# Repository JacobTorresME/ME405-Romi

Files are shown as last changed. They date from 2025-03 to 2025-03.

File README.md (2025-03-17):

# Mechatronics Romi Project
A MycroPython-based Romi robot project using an STM32 board (via the 'pyb' module). 

**By Jacob Torres and Carter Josef**

## Table of Contents
- [Overview & Objectives](#overview--objectives)
- [Features](#features)
- [Bill of Materials (BOM)](#bill-of-materials-bom)
- [Electrical Design](#electrical-design)
- [Mechanical Design](#mechanical-design)
- [Motor Characterization](#motor-characterization)
- [Code Description](#code-descriptions)
  1. [Scheduler](#scheduler)
  2. [Tasks](#tasks)
  3. [Driver Classes](#driver-classes)
- [Finite State Machines](#finite-state-machines)

---

## Overview & Objectives

### Project Obejctive

**Goal**: The primary goal of this project was to design, build, and program a robot, called Romi, capable of autonomously completing a predefined course using cooperative multitasking

**Tasks**:
- Detecting and following a black line while making the necessary route adjustments.
- Navigating through a grid/tunnel section using heading information from a onboard IMU.
- Detecting and responding to obstacles using bump sensors to detect collisions.

**Solution**: We implemented a line sensor, bump sensor, and IMU heading information to navigate and complete the track.

**Track Reference**:

Track

**Romi can**:
  1. Follow black lines using IR sensors and a PID controller.  
  2. Navigate a grid/tunnel utilizing IMU headings and encoder distance data.  
  3. Detect collisions using bump sensors and respond accordingly.

**Romi Setup**:
The Romi has to be placed inside of the starting box facing the first line. The board remians plugged into the computer until the porgram has initialized successfully. Once initialization is complete, we unplugged Tomi from the computer, pressed the blue button on the Nucleo, and alllowed it to run on the course independently.

**Romi**:

Romi

**Demonstration**:

[YouTube Demo Video](https://www.youtube.com/watch?v=X8mRvTR4OUs)

## Features
1. **Line-Following**: Infrared sensor and a PID controller assist Romi in ramaining on track.
2. **Grid/Tunnel Navigation**: To move in cardinal directions, encoders and IMU-based heading were used.
3. **Collision Detection**: Bump sensors triggered by collision allow Romi to detect and maneuver obstacles encountered.
4. **MicroPython**: A STM32-based microcontroller runs python and leverages `cotask` and `task_share` for real-time task scheduling. Additionally, tasks are split into distinct `.py` modules to enable cooperative multitasking.
5. **Custom Mounts**: Custom 3D printed line sensor and bump senser mounts were implemented to allow for proper installation and usage.

## Bill of Materials (BOM)
| Item | Quantity | Description | Link / Source |
|---|---|---|---|
| Pololu Romi Chassis | 1 | Romi base with 2 DC motors | [Pololu Romi](https://www.pololu.com/category/203/romi-chassis-kits)  |
| STM32-L476RG | 1 | MicroPython-compatible MCU | [STM32 Board](https://estore.st.com/en/products/evaluation-tools/product-evaluation-tools/mcu-mpu-eval-tools/stm32-mcu-mpu-eval-tools/stm32-nucleo-boards/nucleo-l476rg.html)  |
| Power Distribution Board & DRV8838 Motor Drivers | 1 | Distributes power and contains two motor drivers  | [Power Distribution Board](https://www.pololu.com/product/3543) |
| BNO055 Sensor | 1 | IMU for orientation | [BNO055](https://www.adafruit.com/product/2472) |
| IR Sensors | 1 | Reflective IR for line sensing  | [IR Sensors](https://www.pololu.com/category/203/romi-chassis-kits) |
| Bump Switches | 2 | Collision sensors | [Left Bump Sensor](https://www.pololu.com/product/3673) [Right Bump Sensor](https://www.pololu.com/product/3674) |
| Dupont Wires | Many | Female to female | [Wires](https://www.amazon.com/dp/B07GCY6CH7?th=1) |

## Electrical Design
The Romi is wirred to an STM32-L476RG Nucleo board. This allows for the integration of multiple sensors and motor controller that facilitate course navigation and obstacle detection. The set up includes:

- Power Source (6 double AA baterries)
- Power Distribution Board
- Encoders
- Bump Sensors
- Motor Drivers
- Line Sensor
- IMU (Inertial Measurement Unit)

A wiring diagram demonstrating how each one of the components above is connect can be seen in the diagrema below

**Wiring Diagram of Romi**

Wirring diagram

This wiring diagram helped us ensure real-time feedback and control, which at the end was a crucial component that allowed Romi to navigate and complete the course. 

## Mechanical Design

The mechanical design modifications to the original Romi chasis were primarily driven by the need to accomodate our long 14mm x 13 line sensor at the front of Romi. This key adjustment lead to one more smaller modification to the bump sensors. All the necessary CAD files for these modifications can be found in the CAD folder at the top of the repository. 

### Line Sensor Mount
Due to our line sensor being 14 mm in length the conventional standoff configuration rendered impractical without additional modifications. To securely mount our line sensor, we 3D printed custom bracket arms, as shown below. These bracket arms allowed us to use the original standoffs and position the line sensor flush with the bottom of Romis chassis and at the very front of Romi for optimal performance. 

**CAD picture of Line-Sensor Arms**

IRsensor

### Bump Sensor Mounts
In adjusting our Romi chassis to accommodate thr line sensor, we inadvertently caused some fitment issues with the bump sensors. The bolts securing the standoffs prevented the bump sensors from sitting flush on top of Romi. Additionally, the bump sensors did not extend far enough past the line sensor, leaving it exposed and failing to detect collisions in these places. To resolve this, we fabricated two custom brackets: an L-shaped bracket and a straight bracket for each of the bump sensors. These brackets allowed the sensors to be mounted securely while ensuring they extended far enough to protect the line sensor and detect obstacles effectively. Furthermore, each bracket was __mm thick, allowing a precise fit above the bolts securing components at the bottom of the Romi chassis. Finally, the combination of both brackets allowed for the bump sensors to remain rigid and in place, including after collision. 

**CAD Picture of Bump Bracket Arms**

Lbrackets
straightbracket

### Romi Assembly
The bracket arms for the line sensors were secured using M2.5 bolts while the bracket arms for the bump sensors were secured using M2.0 bolts. Additionally, the bump sensors used washers and M2.0 nuts to fully secure the bump sensors onto the Romi chassis. 

## Motor Characterization
To properly control the DC motors we performed characterization tests for the left and right motors, to find the motors gain, time constant, and minimal effort required to make the motor turn. The tests consisted of producing a step response by setting the percent PWM going to each of the motors from 0% to 70%. We collected the Time, Position, and Velocity of each of the motors, at a sampling rate of 1000Hz, and saw how the properties of the motor evolved over time.

To find each motors gain and startup effort we extracted the steady-state velocity from the last data points of each run on the Velocity vs. Time plots. We then created a scatter plot of the Steady-State Velocity vs. Input Voltage and calculated the best fit line using linear regression. The slope of this line represented the motor gain and the y-intercept of the line represented the minimum voltage required to overcome static friction (startup effort). The Motor Gain and Startup Effort plots are shown below.

**Motor Gain and Minimum Effort Required Plot**

Motor Gain Right

Motor Gain Left

To calculate the each of the motors time constant (τ) we used a the following logarithmic transformation

$\ln \left( 1 - \frac{\omega}{\omega_{\max}} \right)$

where:

$$
\omega \text{ is the motor velocity at time } t
$$

$$
\omega_{\max} \text{ is the steady-state velocity}
$$

From here a linear regression was performed on the transformed data were the negative inverse of the slope was taken to determine each of the motors time constants (τ). The Linearized Output vs. Time plots are shown below. 

**Linearized Output vs. Time Plot**

Linerized Right

Linerized Left

The resulting values determined in this step are shown below

| Motor | Motor Gain (rad/V*s) | Time Constant (s) | Minimum Effort Required (V) |
|---|---|---|---|
| Left  | 6.73 | 0.0721 | 0.61 |
| Right | 6.39 | 0.0698 | 1.01 |

## Block Diagram of the System

The following diagram is a visual representation of the control diagram used for Romi. We opted for the cascaded control system. We used a PID controller for each wheel. The input to this is a motor speed. The encoder provides feedback to ensure that each wheel is spinning at the desired rate. Linear velocity and angular velocity of Romi are decoupled into individual wheel velocities. This is checked with a PID controller using the IMU and line sensor for feedback.

System block diagram

## Task Diagram

The following diagram is a visual representation of the different tasks within our program. Each task is discussed in further detail below.

Task Diagram

## Code Descriptions

### Scheduler

#### **main.py**

**Purpose**:
`main.py` is the central coordinating file that initializes shared data structures and creates task objects. In addition, it uses cooperative multitasking through the use of `cotask` to "hop" between tasks. Most importantly, this is were you set up each individual task and manage which tasks run, in what order, and how frequentely. 

**Inner Workings**:
1. **Share Initialization**
   - At the top of `main.py`, there is multiple lines of code that create shared variables using `task_share.Share()`.
   - Examples are shown below:
   ```python
   yaw_rate       = task_share.Share('f', thread_protect=False, name="yaw_rate")
   omega_r        = task_share.Share('f', thread_protect=False, name="omega_r")
   run_flg        = task_share.Share('i', thread_protect=False, name="run_flg")
   ...
   ```

   Each of these labels is a global data structute for inter-task communication. An example of this is, `yaw_rate` is a float that tasks can write to (e.g., line-following logic) and read from (e.g., motor tasks)

2. **Task Creation**
   - `main.py` also instantiates each task object from the corresponding task file
   - This file gives each task object 3 things:
     - A priority (the order in which the schedular checks the task)
     - A period (How oftern they should run, in milliseconds)
     - A list of shared variables that they need to read from or write to.
   - For example:
     ```python
     task2 = cotask.Task(task2_right_motor.generator, name="Task_2",
                        priority=4, period=10, profile=True, trace=False, 
                        shares=(omega_r, run_flg))
     ```
3. **Schedular Setup**
   - After creating tasks, `main.py` appends each one to `cotask.task_list` and then calls `cotask.task_list.pri_sched()`. This runs a infinite loop that continously calls each task's generator function in order of priority, handling and executing multiple tasks at the same time behind the scenes.

4. **Exception Handling and Cleanup**
   - The file wraps the scheduling call in a `try-except` block to catch runtime erros and `KeyboardInterrupt` that stops the program. When a error occurs, it disables the motors and prints a message exiting safely. 

**Table of Shared Variables**
| Variable | Type | Description |
|---|---|---|
| `yaw_rate` | *float* | Desired yaw rate (turning speed) for steering. |
| `omega_r` / `omega_l` | *float* | Angular velocity commands for the right and left motors, respectively. |
| `run_flg` | *int* | Flag indicating whether the motors should be running (`1`) or stopped (`0`). |
| `grid_flg` | *int* | Signals the robot to enter or exit grid/tunnel navigation logic. |
| `fwd_flg` | *int* | Controls movement: **1 = Forward**, **2 = Backward**, **0 = Idle**. |
| `line_follow_flg` | *int* | Enables (`1`) or disables (`0`) line-following logic. |
| `line_flg` | *int* | Indicates whether a line was **lost (1)** or **found (0)** (used by Master Mind for transitions). |
| `line_value` | *int* | Numeric data about line detection (**0 = On-line**, **1 = Off-line**). |
| `bump_flg` | *int* | Collision detection flag, set to **`1`** when a bumper switch is triggered. |

These shares are a key component that enables tasks to communicate in a cooperative manner.

---

### Tasks

Each one of these tasks use a **Finite State Machine** within each of their `generator()` functions. Each tasks `generator()` function starts typically with a `S0_STANBY`, `S1_RUN`, etc., and transitions occur based on flags or sensor readings.  

#### **1. MM.py (Master Mind)**

- **Purpose**: Acts as the main handler, it implements a FSM machine to control overall behavior
- **FSM State Breakdown**
1. `S0_STANDBY`:
    - Waits for a user button press or for the `run_flg` to become `
    - One triggered, it moves to finding the.
2. `S1_FIND_LINE`:
    - Tells the motors to drive straight until the Infrared sensors detect a line.
    - Once a line is found it sets `line_follow_flg = 1` and transitions.
3. `S2_LEVEL_1` (Line Follow Mode)
    - Starts the line-following action. Monitors `line_flg` to see if it has lost the line or detects an intersection, moves to next state.
    - If a the `bump_flg = 1` (collision occurs, it transitions to a collision handling state.
4. `S3_GRID_LEVEL`
    - Sets `grid_flg = 1` and allows **grid_task.py** to take over. This may occur when the robot has traveled a certain distance or reached a marker.
    - Exits the state once the grid/tunnel section is done. 
5. `S4_EXIT_TUNNEL`
    - Handles the logic when leaving the tunnel or grid area. It check the `line_value` variable to find a line.
6. `S5_HITTING_WALL`
    - A state that keeps driving forward until the bump sensors are triggered.  
    - When the collision occurs, sets `bump_flg = 1`; transitions to next state.
7. `S6_MOV_BACK`  
     - Moves backward a certain distance (setting `fwd_flg = 2`).  
     - When done, transitions to the next state.
8. `S7_TURN_NORTH`  
     - Uses IMU heading to rotate Romi back north.  
     - When the heading is aligned, transitions to next state.
9. `S8_DRIVE_NORTH`  
     - Drives Romi north and uses encoders to measure distance.  
     - Moves to the next state upon reaching a certain distance.
10. `S9_TURN_WEST`  
      - Another heading-based rotation points Romi west.  
      - Waits until heading is correct, then transitions to next state.
11. `S10_DRIVE_WEST`  
      - Drives west for a set distance using the encoders to measure distance traveled.  
      - Moves to the next state upon reaching a certain distance.
12. `S11_TURN_SOUTH` / `S12_DRIVE_SOUTH`  
      - These states align the robot south and drive it, eventually returning to the starting point.

- **Key Variables**  
  - `run_flg` to see if it should run or not.  
  - `bump_flg` for collisions.  
  - `line_flg` / `grid_flg` to move between line follow and grid tasks.  
  - `fwd_flg` sets forward or backward motion.
  - `yaw_rate` or `omega_r/l` for controlling turning or speed in each state.

- **How it Works**
  - Each Finite State Machine state in the generator function checks relevant flags/sensors.  
  - If conditions are met it transitions to the next state.
  - This set up allows Master Mind to set a step by step process for Romi from initial placement all the way back to the start.

#### **2. grid_task.py**

- **Purpose**: This task is in charge of the grid/tunnel navigation portion, using an internal FSM to perform heading adjustments and distance-based travel.
- **FSM State Breakdown**
1. `S0_INIT`  
     - Reads and stores the robot’s current IMU heading.  
     - Waits for `grid_flg == 1`.
2. `S1_STANDBY`  
     - Idle state, monitoring `grid_flg`.
     - If `grid_flg` becomes 1 it proceeds to the next state.
3. `S2_TURN_SOUTH`  
     - Alings Romis heading to 2880, representing south.  
     - Continuously reads the heading from the IMU
     - Updates `yaw_rate` using a small heading PID (or direct turn logic).  
     - Once aligned, sets `fwd_flg = 1`and transitions to the next state.
4. `S3_DRIVE_SOUTH`  
     - Moves forward until encoders indicate a certain distance.  
     - Once the distance is reached it transitions to the next state.  
5. `S4_TURN_WEST`
     - A final aligment step. Waits until heading is 4320, correspoding to West.
     - Sets `fwd_flg = 1` before returning to standby state.
     - Once the tunnel ends it sets `grid_flg = 0` to exit grid mode.
  
- **Key Variables**  
  - `heading` from `IMU.py`.  
  - `left_start` / `right_start` for storing initial encoder positions.  
  - `grid_flg` to activate or deactivate the grid task.  
  - `yaw_rate` sets turning commands.

- **How It Works**  
  - Each time the generator runs, it checks its current FSM state.  
  - Aligns Romis heading and drives a fixed distance in that prescribed heading.  
  - Moves to the next state when the target heading or distance is achieved.
 
#### **3. line_task.py**

- **Purpose**: This task is in charge of performing line-following using a Infrared sensor data and a PID for steering correction.
- **FSM State Breakdown**  
1. `S0_STANDBY`
   - Waits for `line_follow_flg == 1`.
2. `S1_RUN`:
   - Actively calculates line offset, feeding a PID to adjust `yaw_rate`.
- **Key Variables**  
  - `line_follow_flg`, `fwd_flg`, `yaw_rate`.  
  - Reads the Infrared sensor centroid from `IR_Array.py`.
- **How It Works**  
  - In the `SO_STANDBY` state it waits to be activated 
  - While it is in `S1_RUN` state, during each cycle run it...
     - Gets the IR centroid.  
     - Error of the centriod (centroid - 7).  
     - Uses a PID to calculate a correction.  
     - The correction is written to `yaw_rate`, which **motorstask.py** uses for left/right speed differences.

#### **4. line_finder.py**

- **Purpose**: The task is in charge of alerting the system when the line is lost or re-found.
- **FSM State Breakdown**
1. `S0_LOOK_FOR_LINE`
    - If the data received from the IR indicates is no line it sets `line_flg = 1` and transitions to the next state.
2. `S1_LOOK_FOR_ACK`  
    - Waits until `line_flg` is cleared, once it is cleared it returns to `S0_LOOK_FOR_LINE`.
- **Key Variables**  
  - `line_flg`, `line_value`.  
- **How It Works**  
  - A set threshhold checks IR readings.  
  - If it crosses this threshold it notifies the rest of the system using the `line_flg` share.  
  - Master Mind or line_task acknowledges by resetting `line_flg`.
 
#### **5. motorstask.py**

- **Purpose**: This task performs closed-loop motor control for left and right wheels. It performs this by reading the encoders and applying PID or a feedfoward gain.
- **FSM**  
1. `S0_STANDBY`
   - Motors remain desabled if `run_flag == 0`
   - If `run_flag == 1` it transitions to the next state   
2. `S1_RUN`
   - Once `run_flg == 1` it reads `omega_r` / `omega_l` from shares
   - It then uses a PID to match actual speeds.
- **Key Variables**  
  - `omega_r`, `omega_l`, `run_flg`.  
  - Encoder velocity feedback from `Encoder.py`.
- **How It Works**  
  - If `run_flg` = 1, calls `Motor.enable()`, enabling the motors.  
  - Compares actual speed to the setpoint.  
  - Uses `PID.py` to calculate an effort and then calls `Motor.set_effort(effort)` to physically drive the motor to the setpoint.
 
#### **6. Collision_Detect_task.py**

- **Purpose**: The purpose of this task it to monitor the bumper states and detect collisions. If a collision occurs it raises a flag for Master Mind to handle.
- **FSM**  
1. `S0_WAIT_FOR_COLLISION`  
    - If a bumper press is detected (`task_Bump.py`), sets `bump_flg = 1`.
    - If `bump_flg = 1` it transitions to the next state.
2. `S1_ACKNOWLEDGE_COLLISION`  
    - Waits until `bump_flg` is cleared by **MM.py**.
    - One `bump_flg` is cleared it then returns to `S0_WAIT_FOR_COLLISION`.
- **Key Variables**  
  - `bump_flg`: collision flag.  
- **How It Works**  
  - During each cycle run it checks if any bumper has been pressed.  
  - If collision occurs and the bumper is pressed it sets `bump_flg = 1` so that Master Mind or other logic can respond.

---

### Driver Classes

#### 1. Encoder.py
- **Purpose**: This class is in charge of interpreting quadrature encoder signals and producing both position and velocity data for each motor.
- **What It Does**:
  - Configures a timer in ENC_AB mode for pins (chA, chB).
  - The `update()` method calculates `delta`, which is equal to, current counter - `prev_count`.
  - Corrects for overflow if the timer wraps.
  - Accumulates `position` and calculates velocity by storing deltas over time.
  - Returns linear positon in mm using wheel geometry through the `get_lin_position` method.
- **Assigned to Help**:
  - **motorstask.py**: uses encoder velocity for PID speed control.
  - **grid_task.py**: uses position to measure distance traveled during tunnel navigation.

#### 2. Motor.py
- **Purpose**: This class offers an interface for controlling a DC motor’s direction and speed though PWM signals.
- **What It Does**:
  - Sets up a timer channel for PWM output, direction pin, and a sleep pin.
  - In the `set_effort(effort)` method it uses the sign of `effort` to set direction and the magnitude for the PWM duty cycle.
- **Assigned to Help**:
  - **motorstask.py**: uses `set_effort()` each cycle to realize the PID output for each motor.
  - **MM.py**: and other tasks can call `enable()` / `disable()` to stop Romi safely.

#### 3. IMU.py
- **Purpose**: This class communicates with the BNO055 IMU sensor to obtain heading, roll, pitch, and calibration data.
- **What It Does**:
  - Uses I²C to configure the BNO055 in a particular mode (e.g., IMU, NDOF).
  - The `read_eul_angles()` method retrieves heading, roll, and pitch Euler angles from internal registers.
  - Provides read/write functions for calibration or operation modes.
- **Assigned to Help**:
  - **grid_task.py**: uses this class for cardinal direction turning.
  - **MM.py**: uses this class for cardinal directions to help with transitions

#### 4. IR_Array.py
- **Purpose**: This class combines multiple IR sensors into one array, providing a centroid.
- **What It Does**:
  - Instantiates multiple `IR_Sensor.py` objects, each referencing a different ADC pin.
  - The `update()` method iterates through each sensor, collects normalized values, computes unweighted (`u_sum`) and weighted (`w_sum`) sums.
  - The `get_centroid()` method returns a float in the 0 to 13 range, indicating line offset.
  - The `find_line()` method returns an integer code, were 0 = on a line, 1 = line lost, 2 = thick line.
- **Assigned to Help**:
  - **line_task.py**: uses this class for continuous line following.
  - **line_finder.py**: uses this class for transitions or intersection detection.

#### 5. IR_Sensor.py
- **Purpose**: This class is a low-level driver class used for a single IR sensor, reading ADC and normalizing it based on black/white calibration.
- **What It Does**:
  - Defines `self.white` and `self.black` thresholds found through `sensor_calibration.py`.
  - The `update()` method reads raw ADC values and then transforms it into a 0–1000 scale.
  - The `read_value()` method returns the raw ADC value.
  - The `read_normal()` method returns a normalized integer value between 0-1000. 
- **Assigned to Help**:
  - **IR_Array.py**: calls this class for each sensor channel
  - **line_finder.py** / **line_task.py**: use data collected from this class to steer or detect line transitions

##### 6. PID.py
- **Purpose**: This class is a generic PID controller used by tasks requiring closed-loop control.
- **What It Does**:
  - In the `control(sp, pv, now)` method it calculates `error = sp - pv` and updates integral and derivative terms.
  - This method returns a control output `cv` used to set motor PWM or yaw rate.
- **Assigned to Help**:
  - **motorstask.py**: with speed or velocity control.
  - **line_task.py**: with offset correction for line following.
  - **grid_task.py**: feeds feeds dir to control heading.

#### 7. task_Bump.py
- **Purpose**: This class sets up the low-level bumper inputs, configuring interrupts or polling to detect contact.
- **What It Does**:
  - Initializes `ExtInt` objects on each bumper pin with `IRQ_FALLING`, meaning it now looks for a falling edge.
  - On interrupt this class calls `set_flag(line)` that sets `self.bump_state = True`.
- **Assigned to Help**:
  - **Collision_Detect_task.py**: uses this driver to read `get_button_state()` or `bump_state` to raise `bump_flg`.
  - **MM.py**: checks if the `bump_flg` indicating a collision needs to override the entire state machine.
 
#### 8. sensor_calibration.py
- **Purpose**: This class is a standalone script for calibrating the IR sensors, it runs offline to establish `white` and `black` thresholds.
- **What It Does**:
  - Logs and prints ADC values as the sensor hovers over black and white surfaces. 
  - User updates **IR_Sensor.py** based on these observed values.
- **Assigned to Help**:
  - **IR_Array.py** / **IR_Sensor.py**: helps these driver classes indirectly to produce accurate line detection data.
  - Important: Not used during normal robot operation—just a calibration tool.

## Finite State Machines

The following diagrams are a visual representation of each tasks finite state machine.

#### MM FSM

MM 11

MM 2

MM 3

#### grid_task FSM

grid task

#### line_task FSM

line follow

#### line_finder FSM

line finder

#### motortask FSM

motor task

#### Collision_Detect_task FSM

collision task

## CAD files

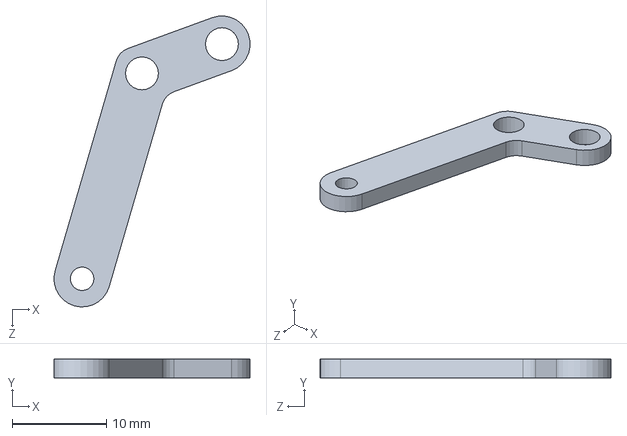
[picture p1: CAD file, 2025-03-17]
Sensor Array Connector.SLDPRT
20.9 x 2.00 x 30.9 mm

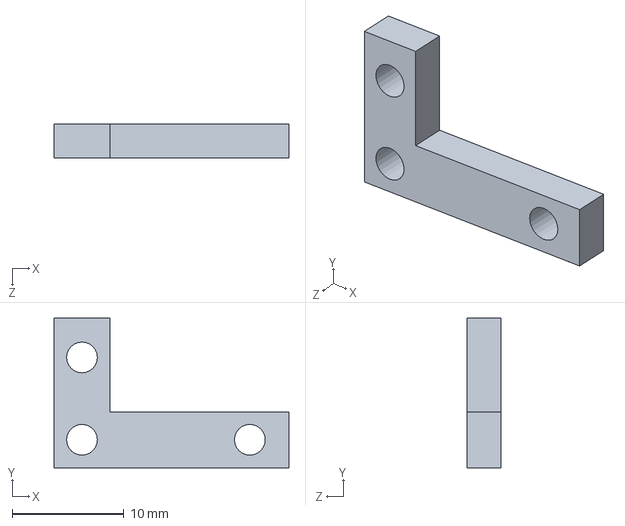
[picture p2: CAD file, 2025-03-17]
BumperL.SLDPRT
21.0 x 13.4 x 3.00 mm

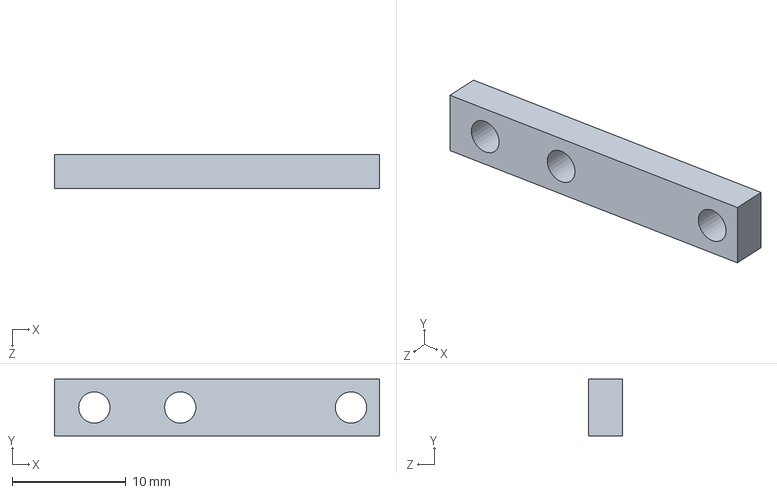
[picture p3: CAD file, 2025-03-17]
Bumper.SLDPRT
28.5 x 5.00 x 3.00 mm

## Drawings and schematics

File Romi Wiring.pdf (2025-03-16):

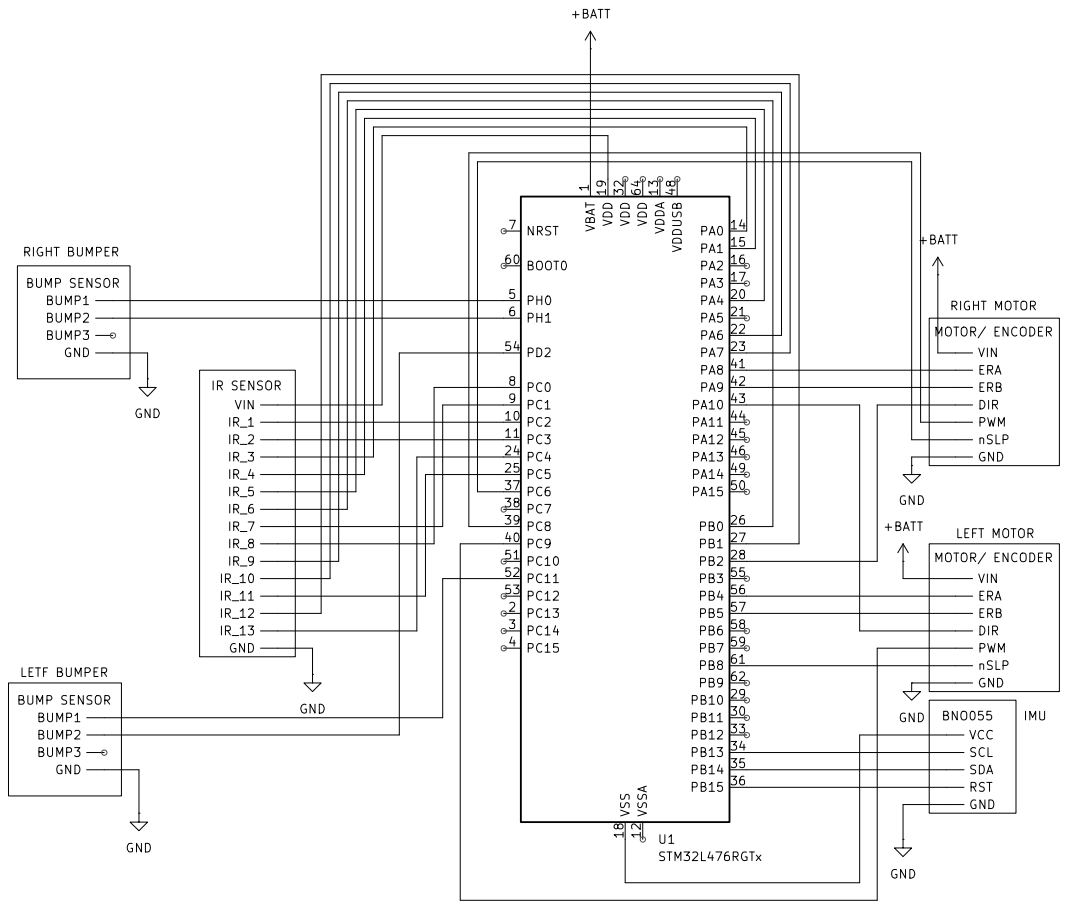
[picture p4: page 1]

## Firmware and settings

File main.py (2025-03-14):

## Main Program for Lab 0x04

import gc
from pyb import Pin, Timer
import cotask
import task_share
from array import array
from Motor import Motor
from Encoder import Encoder
from time import ticks_us, ticks_diff, sleep
from motorstask import motor_task
from IR_Array import IR_Array
from line_task import line_task
from PID import PID
from MM import MM
from IMU import IMU
from task_IMU import task_IMU
from grid_task import grid_task
from line_finder import line_finder
from task_Bump import Bumper
from Collision_Detect_task import collision_detection

# Iniate all motors and sensors
# Motors
Left_Motor = Motor(4, Pin.cpu.C9, Pin.cpu.A10, Pin.cpu.B8)
Right_Motor = Motor(3, Pin.cpu.C8, Pin.cpu.B2, Pin.cpu.C6)
K_l = 6.73 # Left Motor constant rad/[s-vot]
K_r = 6.39 # Right Motor Constant radd/(s-volt)
# Encoders
Left_Encoder = Encoder(Timer(3, period=0xFFFF, prescaler=0), 
                       Pin.cpu.B4, Pin.cpu.B5)
Right_Encoder = Encoder(Timer(1, period=0xFFFF, prescaler=0), 
                         Pin.cpu.A8, Pin.cpu.A9)
# Line Sensor
line_sensor = IR_Array()

# IMU
# Set up Pins for IMU
Pin(Pin.cpu.B10, mode = Pin.OUT)
Pin(Pin.cpu.B11, mode = Pin.OUT)
IMU_RST = Pin(Pin.cpu.B15, mode = Pin.OUT)
Pin(Pin.cpu.B13, mode = Pin.ALT, alt = 4)
Pin(Pin.cpu.B14, mode = Pin.ALT, alt = 4)


# Create an IMU object
my_IMU = IMU(IMU_RST)

# Reset Romi for safe measure
my_IMU.reset()

# Place IMU into fusion mode
my_IMU.choose_mode('IMU')

# Create a data list with all of the calibration coefficients
data_list = [227, 255, 47, 0, 238, 255, 22, 3, 20, 255, 8, 3, 0, 0, 0, 0, 0, 0, 232, 3, 38, 2]
my_IMU.write_cal_coefficients(data_list)

print("hello")
print(my_IMU.read_cal_status())
data = my_IMU.read_cal_coefficients()
sleep(0.1)
data_list2 = list(data)
print(data_list2)

heading, roll, pitch = my_IMU.read_eul_angles()
print(f"heading: {heading}, roll: {roll} pitch: {pitch}")

# PIDs
IMU_PID = PID(0.004, 0, 0, 0)
line_sensor_PID = PID(0.6, 0.06, 0.0, 0) #0.6 .065, .4 .08
left_motor_PID = PID(10, 10, 0, 100/(K_l*4.5))
right_motor_PID = PID(10, 10, 0, 100/(K_r*4.5))
# Misc Variables
velocity = 0.2

# Creating bumper objects
Bump_sensor = Bumper()

# Initiate Task Objects
task1_MM = MM(velocity, Left_Encoder, Right_Encoder, my_IMU, IMU_PID)
task2_right_motor = motor_task(Right_Motor, Right_Encoder,K_r, right_motor_PID)
task3_left_motor = motor_task(Left_Motor, Left_Encoder, K_l, left_motor_PID)
task4_grid = grid_task(my_IMU, IMU_PID, Left_Encoder, Right_Encoder)
task5_line_follow = line_task(line_sensor, line_sensor_PID)
task6_line_finder = line_finder(line_sensor)
task7_wall_task = collision_detection(Bump_sensor)


# This code creates a share, a queue, and two tasks, then starts the tasks. The
# tasks run until somebody presses ENTER, at which time the scheduler stops and
# printouts show diagnostic information about the tasks, share, and queue.
if __name__ == "__main__":
    print("Testing ME405 stuff in cotask.py and task_share.py\r\n"
          "Press Ctrl-C to stop and show diagnostics.")

    # Create a shares to pass between tasks
    yaw_rate = task_share.Share('f', thread_protect=False, name="yaw_rate")
    omega_r = task_share.Share('f', thread_protect=False, name="omega_r")
    omega_l = task_share.Share('f', thread_protect=False, name="omega_l")
    run_flg = task_share.Share('i', thread_protect=False, name="run_flg")
    grid_flg = task_share.Share('i', thread_protect=False, name="grid_flg")
    fwd_flg = task_share.Share('i', thread_protect=False, name="fwd_flg")
    line_follow_flg= task_share.Share('i', thread_protect=False, name="line_follow_flg")
    line_flg = task_share.Share('i', thread_protect=False, name="line_flg")
    line_value = task_share.Share('i', thread_protect=False, name="line_value")
    bump_flg = task_share.Share('i', thread_protect=False, name="bump_flg")
    

    # Create the tasks. If trace is enabled for any task, memory will be
    # allocated for state transition tracing, and the application will run out
    # of memory after a while and quit. Therefore, use tracing only for 
    # debugging and set trace to False when it's not needed
    task1 = cotask.Task(task1_MM.generator, name="Task_1", priority=10, period=10,
            profile=True, trace=False, shares=(yaw_rate, omega_r, omega_l, 
                    grid_flg, fwd_flg, run_flg, line_follow_flg, line_flg, line_value, bump_flg))
    
    task2 = cotask.Task(task2_right_motor.generator, name="Task_2",
                        priority=4, period=10, profile=True, trace=False, 
                        shares=(omega_r, run_flg))
    task3 = cotask.Task(task3_left_motor.generator, name="Task_3", priority=4, period=10,
            profile=True, trace=False, shares=(omega_l, run_flg))
    task4 = cotask.Task(task4_grid.generator, name="Task_4", priority=4, period=10,
            profile=True, trace=False, shares=(yaw_rate, grid_flg, fwd_flg))
    task5 = cotask.Task(task5_line_follow.generator, name="Task_5", priority=3, period=10,
            profile=True, trace=False, shares=(line_follow_flg, yaw_rate, fwd_flg))
    task6 = cotask.Task(task6_line_finder.generator, name="Task_6", priority=1, period=10,
            profile=True, trace=False, shares=(line_flg, line_value))
    task7 = cotask.Task(task7_wall_task.generator, name="Task_7", priority=9, period=10,
            profile=True, trace=False, shares=(bump_flg))
    
    cotask.task_list.append(task1)
    cotask.task_list.append(task2)
    cotask.task_list.append(task3)
    cotask.task_list.append(task4)
    cotask.task_list.append(task5)
    cotask.task_list.append(task6)
    cotask.task_list.append(task7)

    # Run the memory garbage collector to ensure memory is as defragmented as
    # possible before the real-time scheduler is started
    gc.collect()

    # Run the scheduler with the chosen scheduling algorithm. Quit if ^C pressed
    while True:
        try:
            cotask.task_list.pri_sched()
        except KeyboardInterrupt:
            print("Keyboard Interrupt")
            Left_Motor.disable()
            Right_Motor.disable()
            break
        except Exception as e:
            Left_Motor.disable()
            Right_Motor.disable()
            print(e)
            break

    # Print a table of task data and a table of shared information data
    print('\n' + str (cotask.task_list))
    print(task_share.show_all())
    # print(task1.get_trace())
    print('')

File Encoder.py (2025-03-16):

from pyb import Timer
from math import pi

class Encoder:
    '''A quadrature encoder decoding interface encapsulated in a Python class'''
    def __init__(self, tim, chA_pin, chB_pin):
        '''Initializes an Encoder object'''
        self.tim = tim # Timer passed from user. Frequency from lecture
        self.tim.channel(1, pin= chA_pin, mode=Timer.ENC_AB) #ERA
        self.tim.channel(2, pin= chB_pin, mode=Timer.ENC_AB) #ERB
        
        self.position = 0 # Total accumulated position of the encoder
        self.prev_count = 0 # Counter value from the most recent update
        self.delta = 0 # Change in count between last two updates
        self.deltas = [0, 0, 0, 0, 0] # list of last 5 deltas
        self.dt = 0 # Amount of time between last two updates
        self.dts = [0, 0, 0, 0, 0] # List of last 5 dts
        self.idx = 0 # Index to place last 5 points in
        self.prev_tim = 0
        self.AR = 0xFFFF # Autoreload Value
        
        self.r_w = 35 # Whell radius in [mm]
        
    def update(self, now):
        '''Runs one update step on the encoder's timer counter to keep
        track of the change in count and check for counter reload'''
        # Calculate Delta
        self.delta = self.tim.counter() - self.prev_count #update delta
        self.dt = now - self.prev_tim # update dt
        
        # Case of underflow
        if self.delta > (self.AR+1)/2:
            self.delta -= (self.AR + 1)
            
        # Case of overflow
        elif self.delta < -(self.AR+1)/2:
            self.delta += (self.AR+1)
        
        self.position += self.delta # Update Position
        self.deltas[self.idx] = self.delta # place delta into list of deltas
        self.dts[self.idx] = self.dt # Place dt into list of dts
        
        # Move the index to current pointer location
        if self.idx < 4:
            self.idx += 1
        else:
            self.idx = 0
            
        self.prev_count = self.tim.counter() # Current count becomes prev count
        self.prev_tim = now # update prev_tim
    
    def get_position(self):
        '''Returns the most recently updated value of position as determined
        within the update() method'''
        return self.position # Units of Ticks
    
    def get_lin_position(self):
        '''Returns most recently updated value of position in mm'''
        return (self.position*2*pi/1440)*self.r_w
    
    def get_velocity(self):
        '''Returns a measure of velocity using the the most recently updated
        value of delta as determined within the update() method'''
        # Calculate and return average velocity over last 5 updates
        return sum(self.deltas)*1_000_000 // sum(self.dts) # Units ticks/sec
    
    def zero(self, now):
        '''Sets the present encoder position to zero and causes future updates
        to measure with respect to the new zero position'''
        self.position = 0
        self.deltas = [0 ,0 ,0, 0, 0]
        self.dts = [0,0,0,0,0]
        self.prev_count = self.tim.counter()
        self.prev_tim = now

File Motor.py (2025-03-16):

from pyb import Pin, Timer

class Motor:
    '''A motor driver interface encapsulated in a Python class. Works with
    motor drivers using seperate PWM and direction inputs such as the DRV8838
    drivers present on the Romi chasis from Pololu.'''
    
    def __init__(self, PWM_ch, PWM_pin, DIR, nSLP):
        '''Initialize a Motor object'''
        self.nSLP_Pin = Pin(nSLP, mode=Pin.OUT_PP, value=0)
        self.DIR_Pin = Pin(DIR, mode=Pin.OUT_PP, value=0)
        self.tim = Timer(8, freq=20000) # Probably shouldn't reinitialize
        self.PWM_Pin = self.tim.channel(PWM_ch, pin=PWM_pin, mode=Timer.PWM)
    
    def set_effort(self, effort):
        '''Sets the present effort requested from the motor based on an input
        value between -100 and 100'''
        
        # Case for effort is positive
        if effort > 0:
            self.DIR_Pin.low() # makes the motor go forward
        # Case for effort is negative
        else:
            self.DIR_Pin.high() # Makes the motor go backward
            
        effort = abs(effort) # Ensure that effort is a positive value
            
        self.PWM_Pin.pulse_width_percent(effort) # Set PWM
    
    def enable(self):
        '''Enables the motor driver by taking it out of sleep mode into brake
        mode'''
        self.nSLP_Pin.high()
    
    def disable(self):
        '''Disables the motor driver by taking it into sleep mode'''
        self.nSLP_Pin.low() 
